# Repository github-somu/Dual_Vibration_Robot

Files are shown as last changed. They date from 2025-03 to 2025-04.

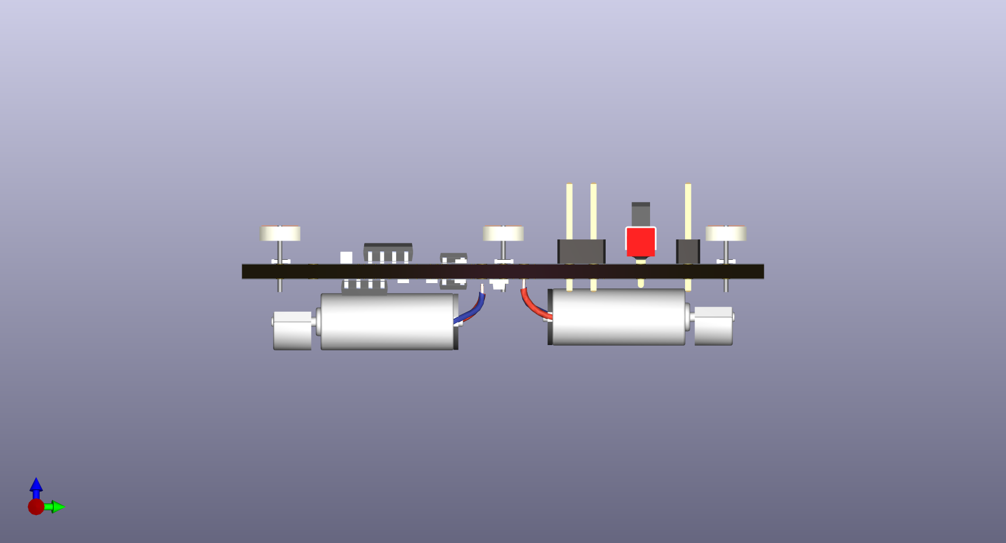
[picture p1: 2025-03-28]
KiCad files/SideViewPCB.png

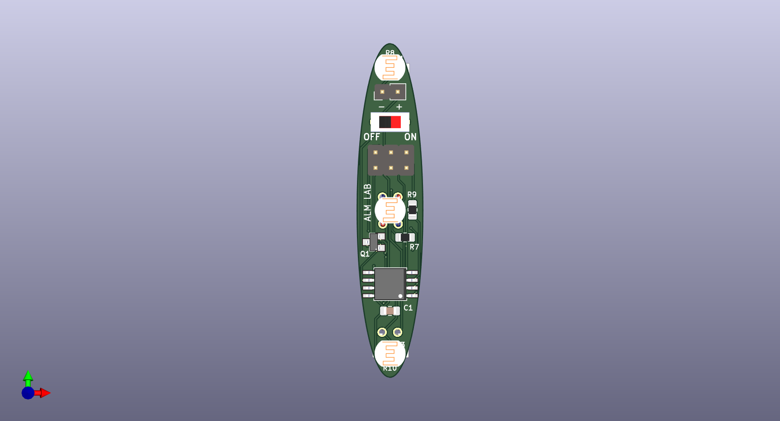
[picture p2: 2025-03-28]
KiCad files/TopViewPCB.png

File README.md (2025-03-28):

# Dual_Vibration_Robot
 This repository contains files related to circuit diagrams, PCB, and 3D models
# Accessing PCB design files and Circuit diagram
Download the KiCad files folder as a .zip file and save it on your computer. After that, extract the folder. Then, the files will open appropriately in KiCad software.

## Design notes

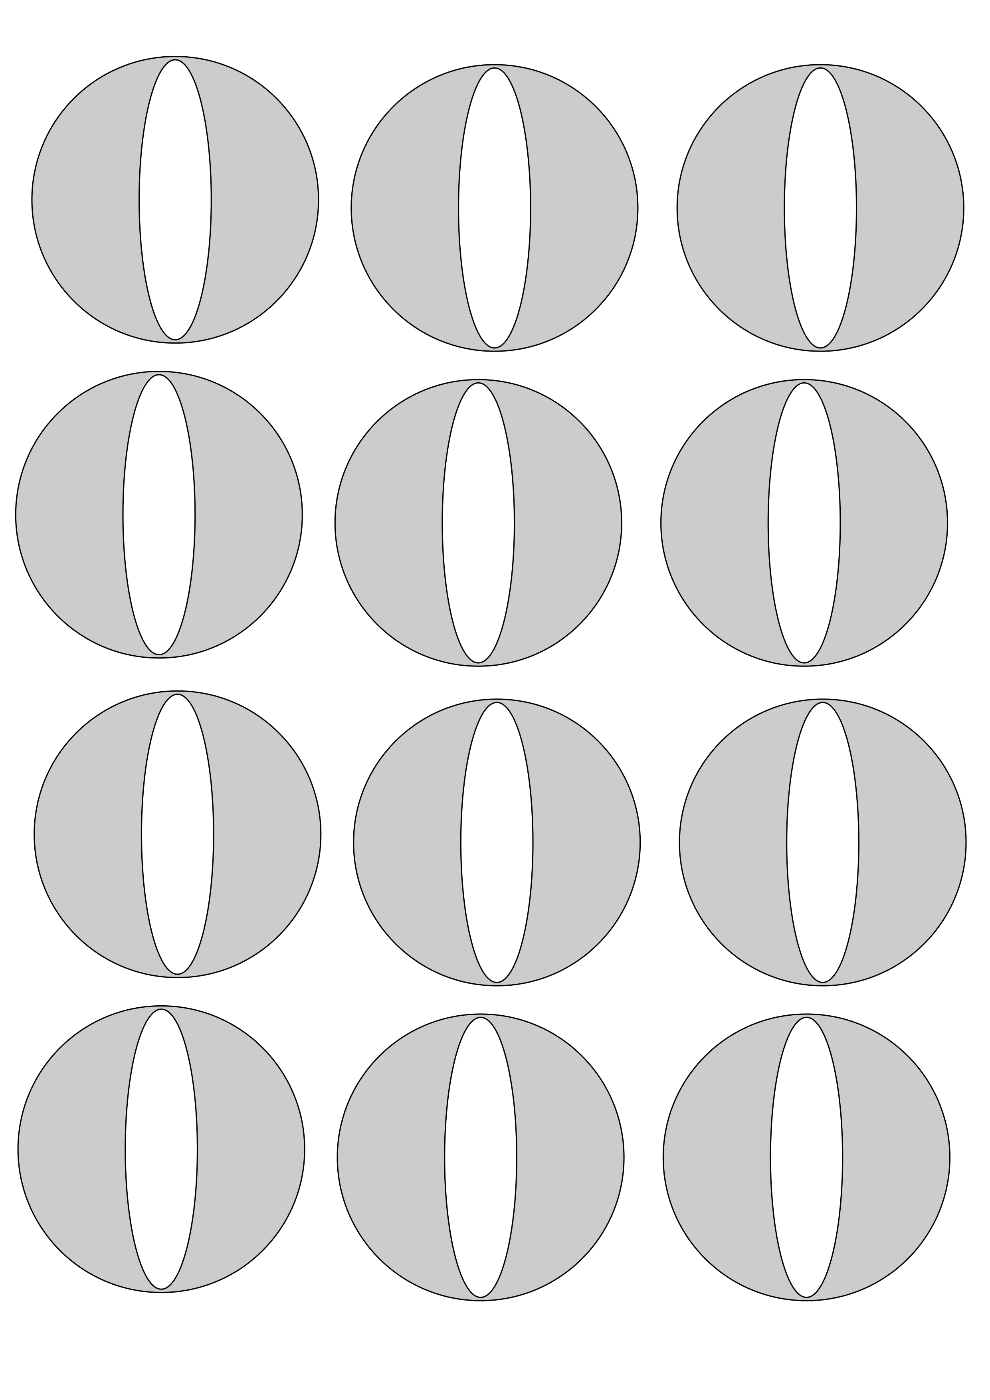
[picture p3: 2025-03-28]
3D_models/Circular_body_paper_cove.png

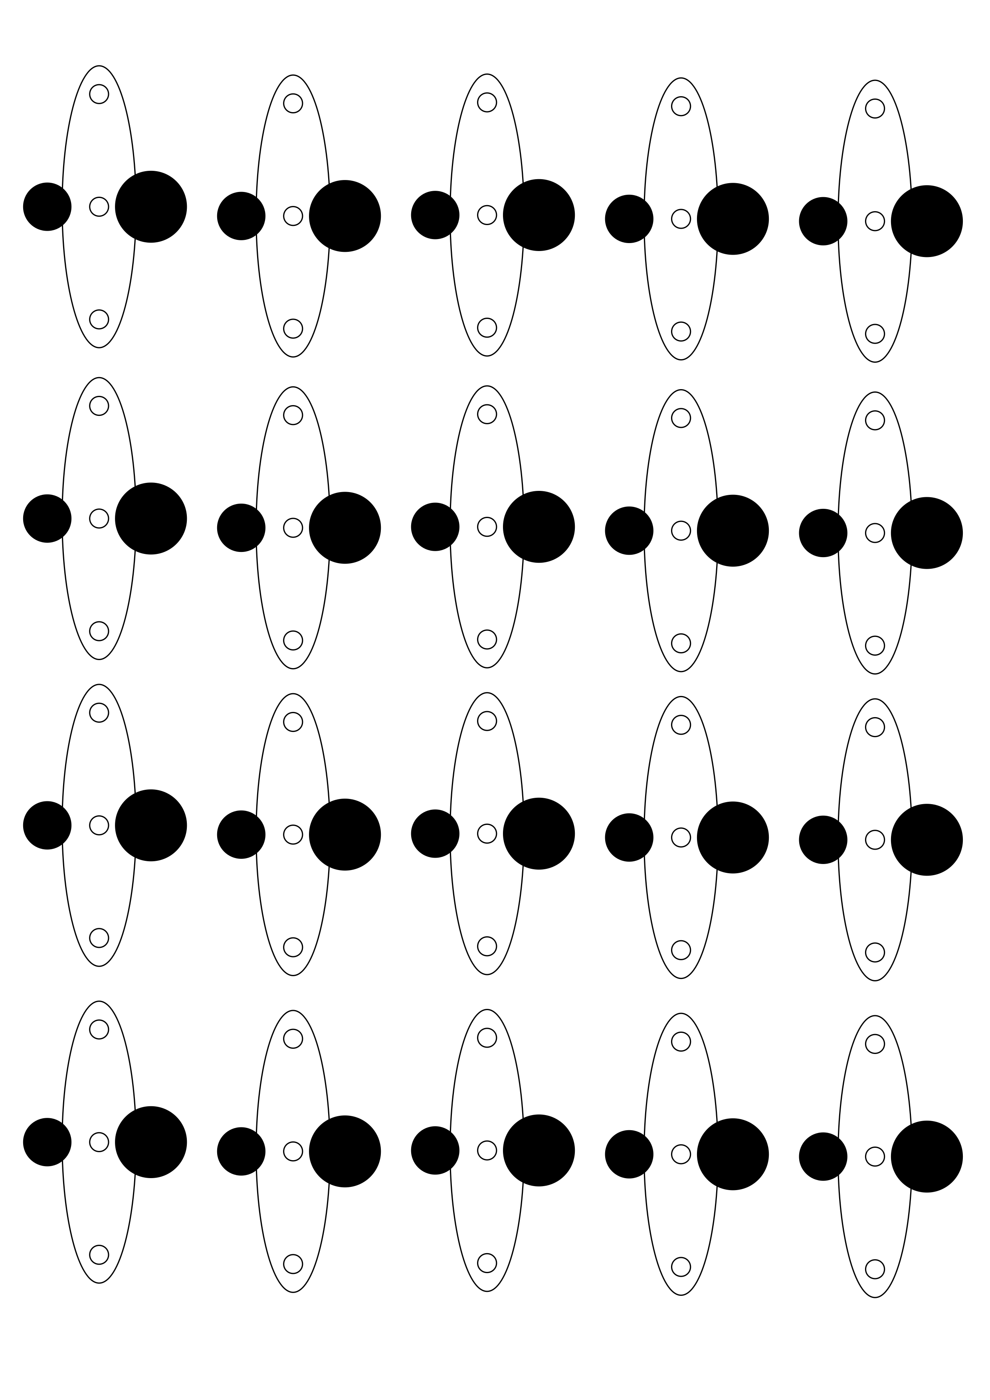
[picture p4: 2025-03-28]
3D_models/Cap_paper_cover.png

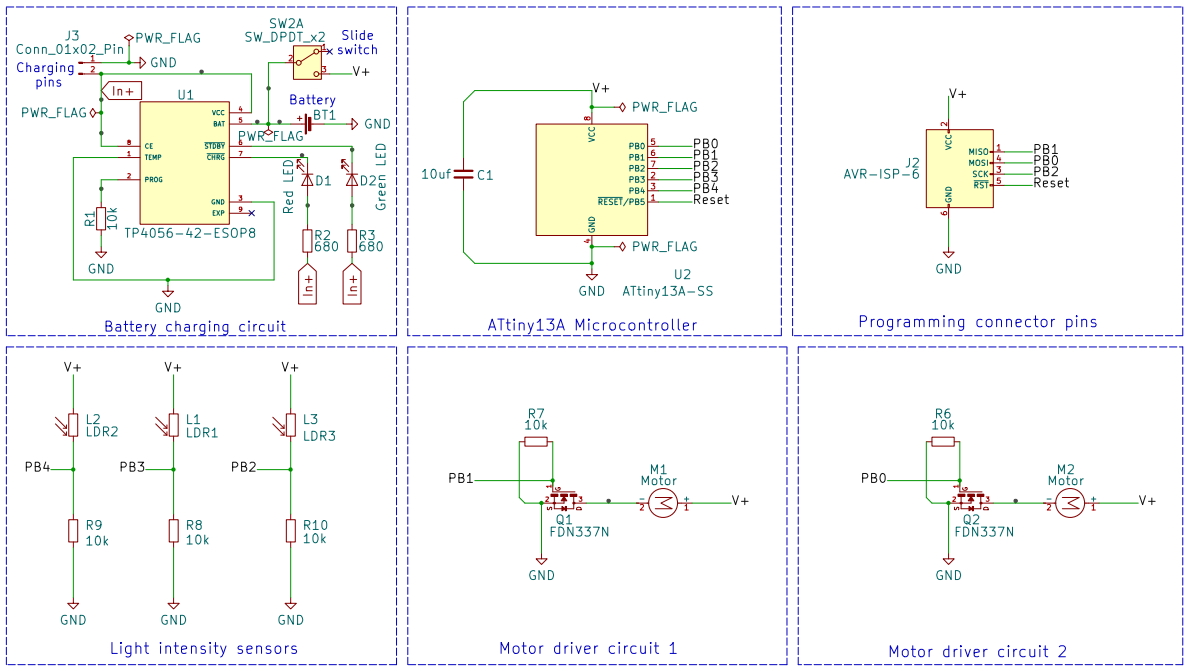
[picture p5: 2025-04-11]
KiCad files/Circuit.png

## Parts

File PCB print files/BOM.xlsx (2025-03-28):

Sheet: SingleMotor
Sample - Bill of Material
Sr. No. | Quantity | Reference | Value | Part Type | PCB Footprint | Manufacturer Part Number/ Generic Part Number[PCB Power] | Manufacturer Name | Description
1 | 5 | R1, R7, R8, R9, R10 | 10 komh, 125mW | Resistor | SMD0805 | GPR080510K | Generic Components - PCB Power | SMD Chip Resistor, 10 kohm, ± 1%, 125 mW, 0805 [2012 Metric], Thick Film, General Purpose
2 | 2 | R2, R3 | 4.7 komh, 125mW | Resistor | SMD0805 | GPR08054K7 | Generic Components - PCB Power | SMD Chip Resistor, 4.7 kohm, ± 1%, 125 mW, 0805 [2012 Metric], Thick Film, General Purpose
3 | 1 | C1 | 10uF, 35V | Capacitor | SMD0805 | GPC0805106-35 | Generic Components - PCB Power | Multilayer Ceramic Capacitors MLCC - SMD/SMT Multilayer Ceramic Capacitors MLCC - SMD/SMT 0805 10uF 35volts *Derate Voltage/Temp
4 | 1 | U2 | NA | ATtiny13A | SOIC127P798X216-8N | ATtiny13A-SU / ATtiny13A-SUR / ATtiny13A-SH / ATtiny13A-SHR | Microchip Technology (https://www.mouser.in/manufacturer/microchip/) | 8-bit Microcontrollers - MCU 1KB In-system Flash 20MHz 1.8V-5.5V
5 | 1 | Q2 | NA | n-MOSFET | SSOT-3 | FDN337N | onsemi / Fairchild | MOSFET SSOT-3 N-CH 30V
6 | 1 | D2 | NA | LED-G | SMD0805 | HSMM-C170 (https://www.mouser.in/ProductDetail/Broadcom-Avago/HSMM-C170?qs=YDL0qNrpDT515hwcVWI5gg%3D%3D) | Broadcom / Avago (https://www.mouser.in/manufacturer/broadcom/) | Standard LEDs - SMD Green Diffused 525nm 120mcd
7 | 1 | D1 | NA | LED-R | SMD0805 | HSMH-H170 (https://www.mouser.in/ProductDetail/Broadcom-Avago/HSMH-H170?qs=Li%252BoUPsLEns3UdNxsKqV%252Bg%3D%3D) | Broadcom / Avago (https://www.mouser.in/manufacturer/broadcom/) | Standard LEDs - SMD 0805 Top Mount Mono-Color ChipLED, AllnGaP Red
8 | 1 | U1 | NA | Battery Charging IC | SOIC127P600X175-9N | TP4056-42-ESOP8 | TOPPOWER(Nanjing Extension Microelectronics) | ESOP-8 Battery Management ICs ROHS

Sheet: DoubleMotor
Sr. No. | Quantity | Reference | Value | Part Type | PCB Footprint | Manufacturer Part Number/ Generic Part Number[PCB Power] | Manufacturer Name | Description
1 | 6 | R1, R6, R7, R8, R9, R10 | 10 komh, 125mW | Resistor | SMD0805 | GPR080510K | Generic Components - PCB Power | SMD Chip Resistor, 10 kohm, ± 1%, 125 mW, 0805 [2012 Metric], Thick Film, General Purpose
2 | 2 | R2, R3 | 3.3 komh, 125mW | Resistor | SMD0805 | GPR08054K7 | Generic Components - PCB Power | SMD Chip Resistor, 4.7 kohm, ± 1%, 125 mW, 0805 [2012 Metric], Thick Film, General Purpose
3 | 1 | C1 | 10uF, 35V | Capacitor | SMD0805 | GPC0805106-35 | Generic Components - PCB Power | Multilayer Ceramic Capacitors MLCC - SMD/SMT Multilayer Ceramic Capacitors MLCC - SMD/SMT 0805 10uF 35volts *Derate Voltage/Temp
4 | 1 | U2 | NA | ATtiny13A | SOIC127P798X216-8N | ATtiny13A-SU / ATtiny13A-SUR / ATtiny13A-SH / ATtiny13A-SHR | Microchip Technology (https://www.mouser.in/manufacturer/microchip/) | 8-bit Microcontrollers - MCU 1KB In-system Flash 20MHz 1.8V-5.5V
5 | 2 | Q1,Q2 | NA | n-MOSFET | SSOT-3 | FDN337N | onsemi / Fairchild | MOSFET SSOT-3 N-CH 30V
6 | 1 | D2 | NA | LED-G | SMD0805 | HSMM-C170 (https://www.mouser.in/ProductDetail/Broadcom-Avago/HSMM-C170?qs=YDL0qNrpDT515hwcVWI5gg%3D%3D) | Broadcom / Avago (https://www.mouser.in/manufacturer/broadcom/) | Standard LEDs - SMD Green Diffused 525nm 120mcd
7 | 1 | D1 | NA | LED-R | SMD0805 | HSMH-H170 (https://www.mouser.in/ProductDetail/Broadcom-Avago/HSMH-H170?qs=Li%252BoUPsLEns3UdNxsKqV%252Bg%3D%3D) | Broadcom / Avago (https://www.mouser.in/manufacturer/broadcom/) | Standard LEDs - SMD 0805 Top Mount Mono-Color ChipLED, AllnGaP Red
8 | 1 | U1 | NA | Battery Charging IC | SOIC127P600X175-9N | TP4056-42-ESOP8 | TOPPOWER(Nanjing Extension Microelectronics) | ESOP-8 Battery Management ICs ROHS

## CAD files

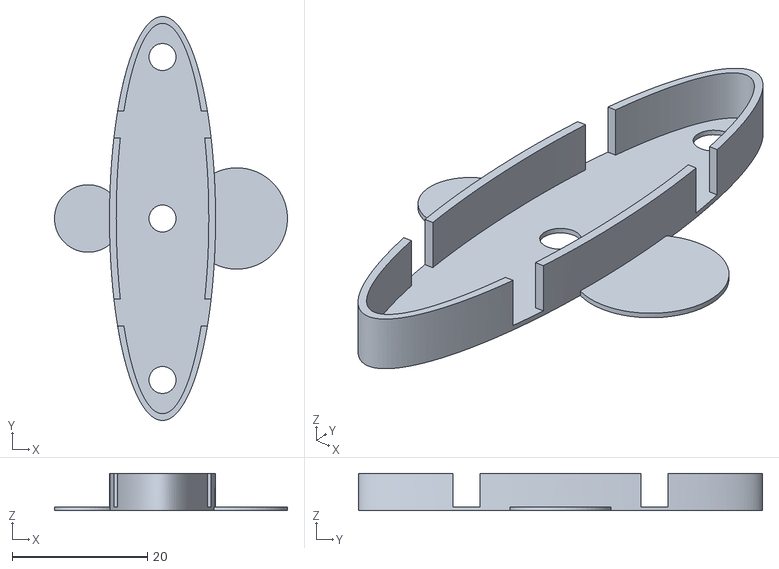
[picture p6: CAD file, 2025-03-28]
3D_models/Cap_DualCircles.stl
34.5 x 59.8 x 5.50

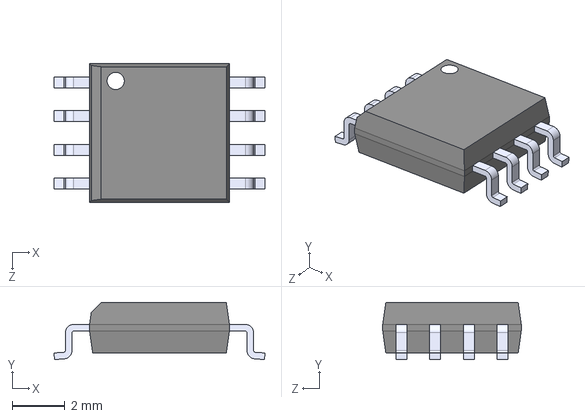
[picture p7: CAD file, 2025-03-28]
KiCad files/ATTINY13A-SSU/ATTINY13A-SSU.step
7.98 x 2.16 x 5.24 mm

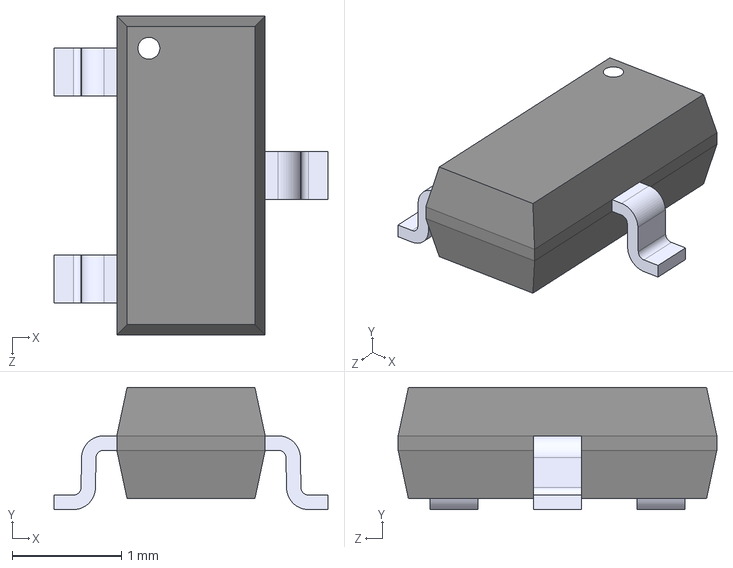
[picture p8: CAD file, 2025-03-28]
KiCad files/FDN337N/FDN337N.step
2.51 x 1.12 x 2.92 mm

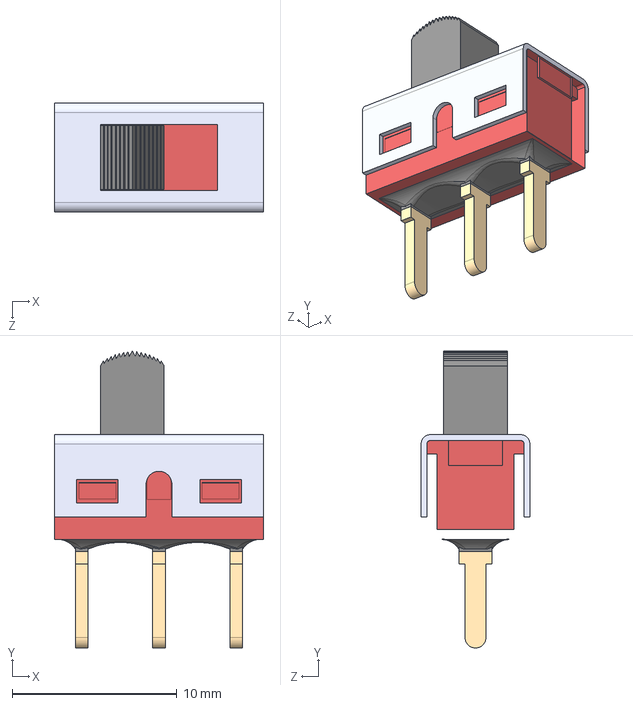
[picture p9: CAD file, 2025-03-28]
KiCad files/STEP files/500SSP1S1M2REA--3DModel-STEP-418109.STEP
12.7 x 18.0 x 6.60 mm

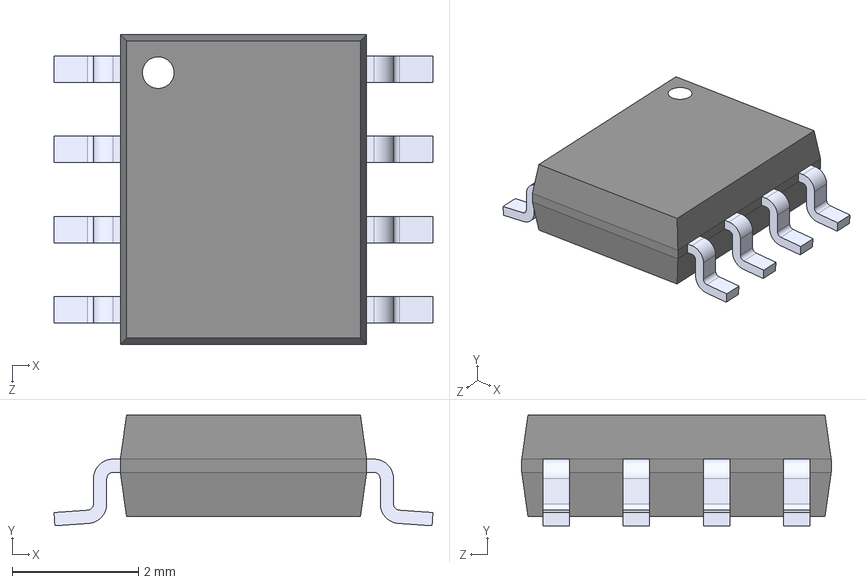
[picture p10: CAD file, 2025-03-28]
KiCad files/TP4056-42-ESOP8/TP4056-42-ESOP8.step
6.00 x 1.75 x 4.90 mm

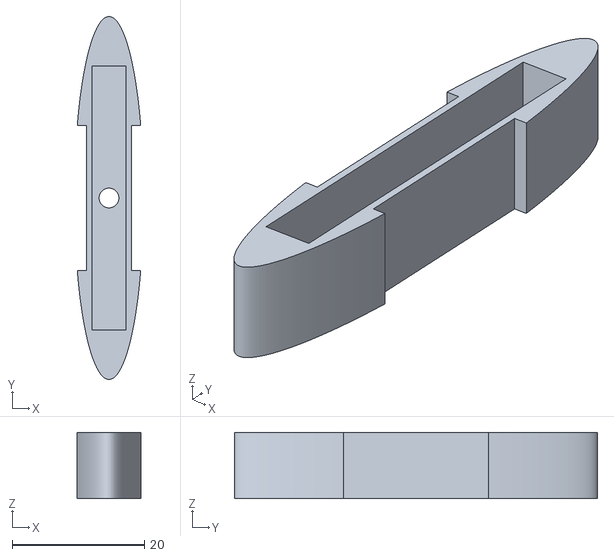
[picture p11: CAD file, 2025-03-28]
3D_models/BattteryHolder_OutwardMotors.stl
9.62 x 55.0 x 10.0

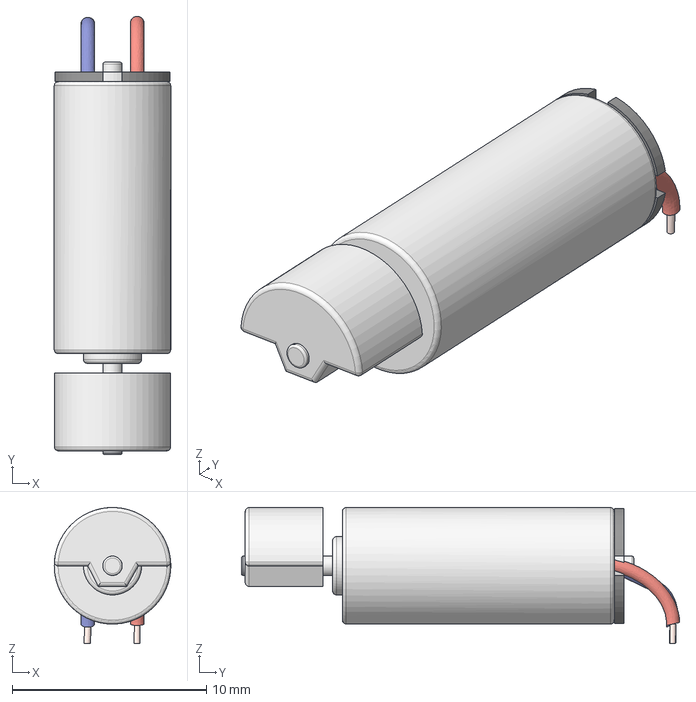
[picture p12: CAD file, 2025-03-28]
KiCad files/STEP files/VibrationMotor v1.step
6.00 x 22.6 x 7.00 mm

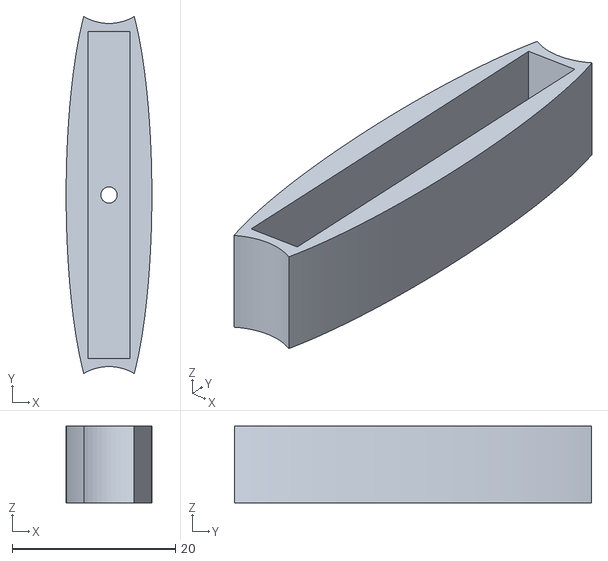
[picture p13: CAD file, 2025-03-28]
3D_models/BatteryHolder_InwardMotors.stl
10.5 x 43.7 x 9.40

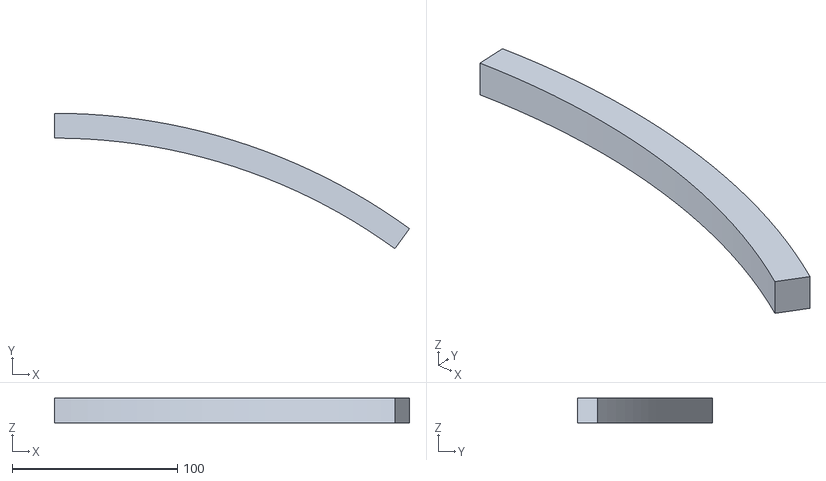
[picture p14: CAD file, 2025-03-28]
3D_models/Boundary_01.stl
214.5 x 81.8 x 15.0

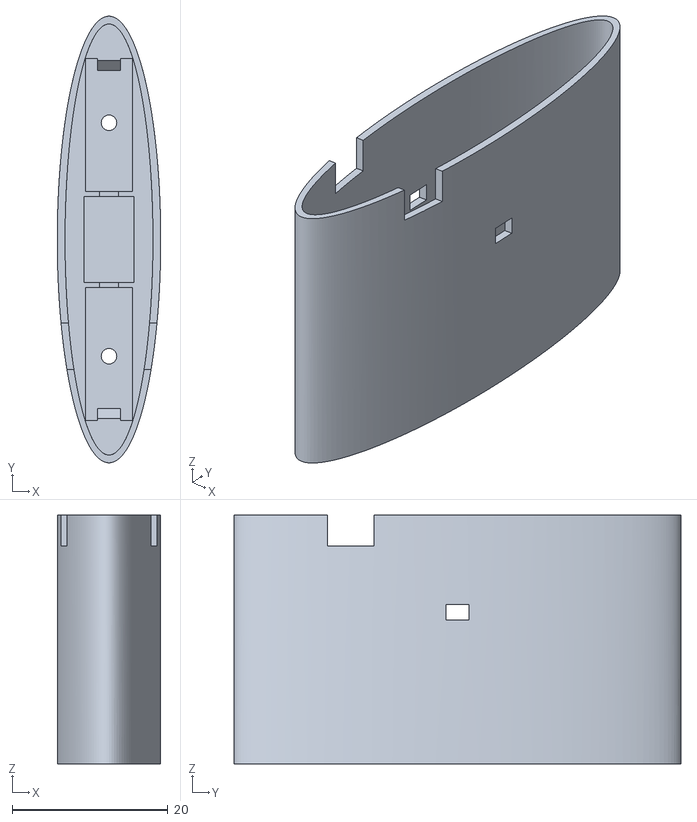
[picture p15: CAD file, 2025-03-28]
3D_models/Body_DualMotor_Inward_Horizontal.stl
13.3 x 57.4 x 32.0

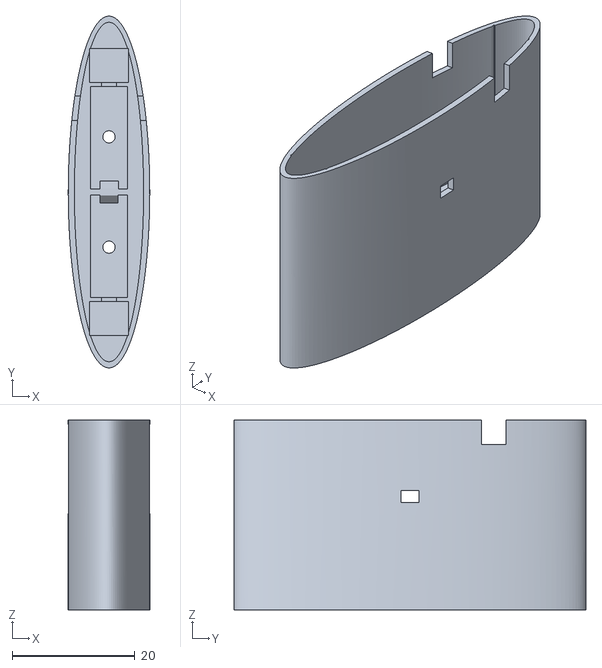
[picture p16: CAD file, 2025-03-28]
3D_models/Body_DualMotor_Outward_Horizontal.stl
13.3 x 57.4 x 31.0

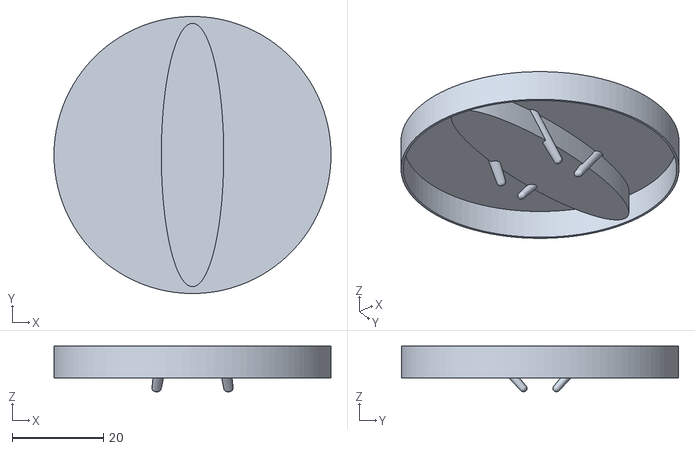
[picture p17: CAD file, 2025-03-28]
3D_models/Legs_Circular.stl
60.8 x 60.8 x 10.0

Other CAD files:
3D_models/Boby_and_BatteryHolder_OutwardMotors.f3d
3D_models/Boundary_Part.f3d
3D_models/Cap_DualCircles.f3d
3D_models/Legs_CircularShape.f3d
3D_models/More_separated_legs v2.f3d

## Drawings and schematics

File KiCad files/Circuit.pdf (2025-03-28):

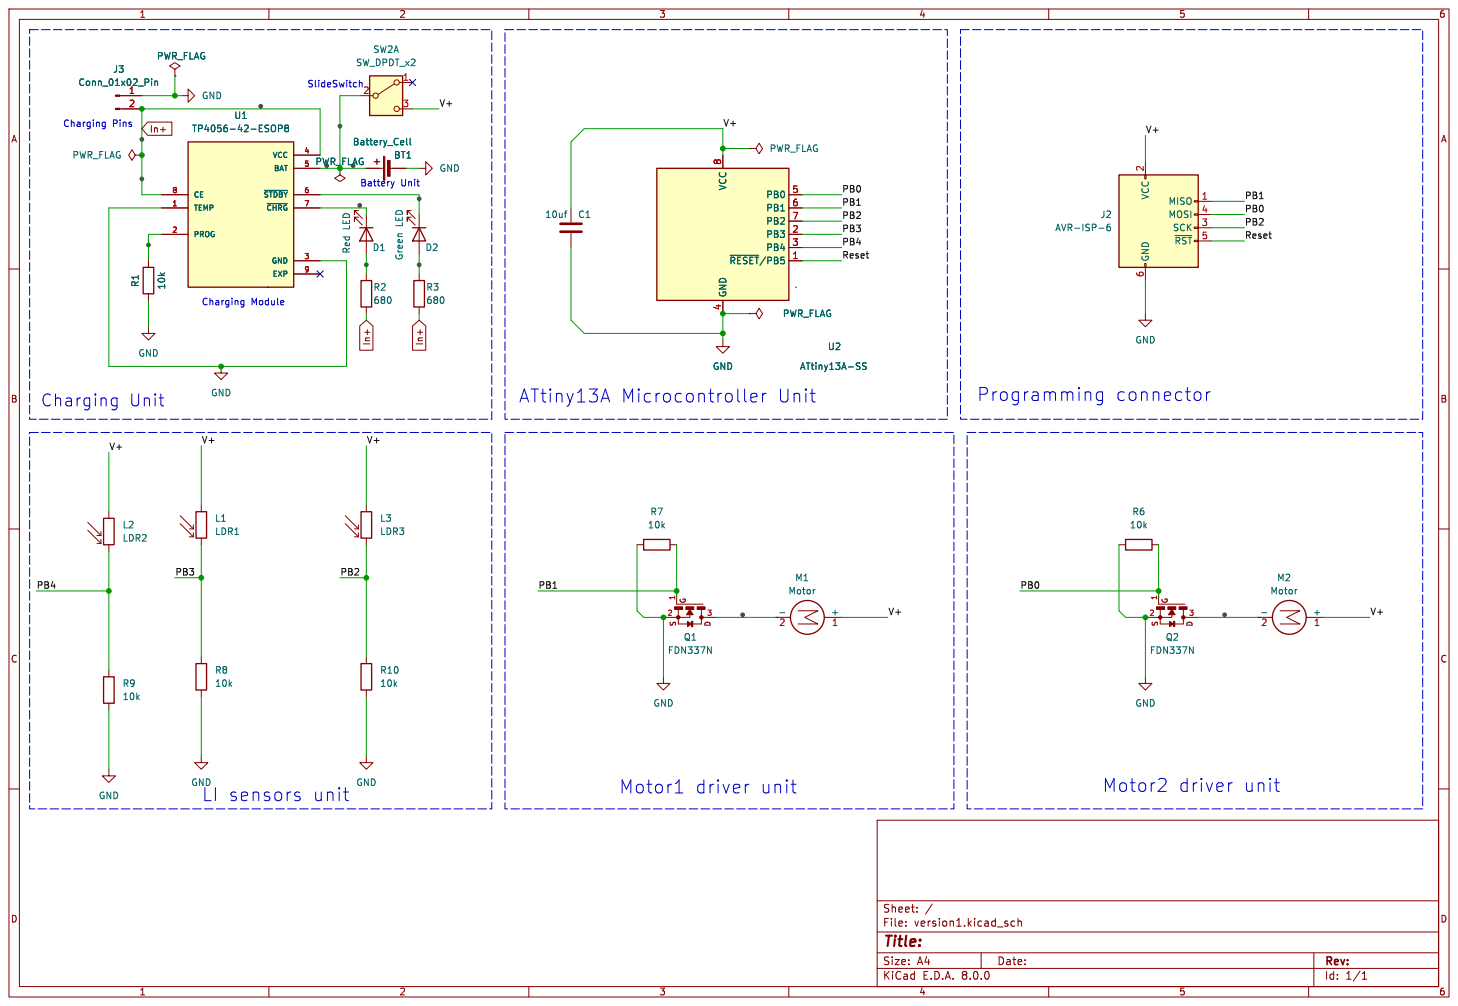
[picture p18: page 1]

2 SCK 3 MOSI 4 ~{RST}5 GND

Id: 1/1 Title: File: version1.kicad_sch Sheet: /

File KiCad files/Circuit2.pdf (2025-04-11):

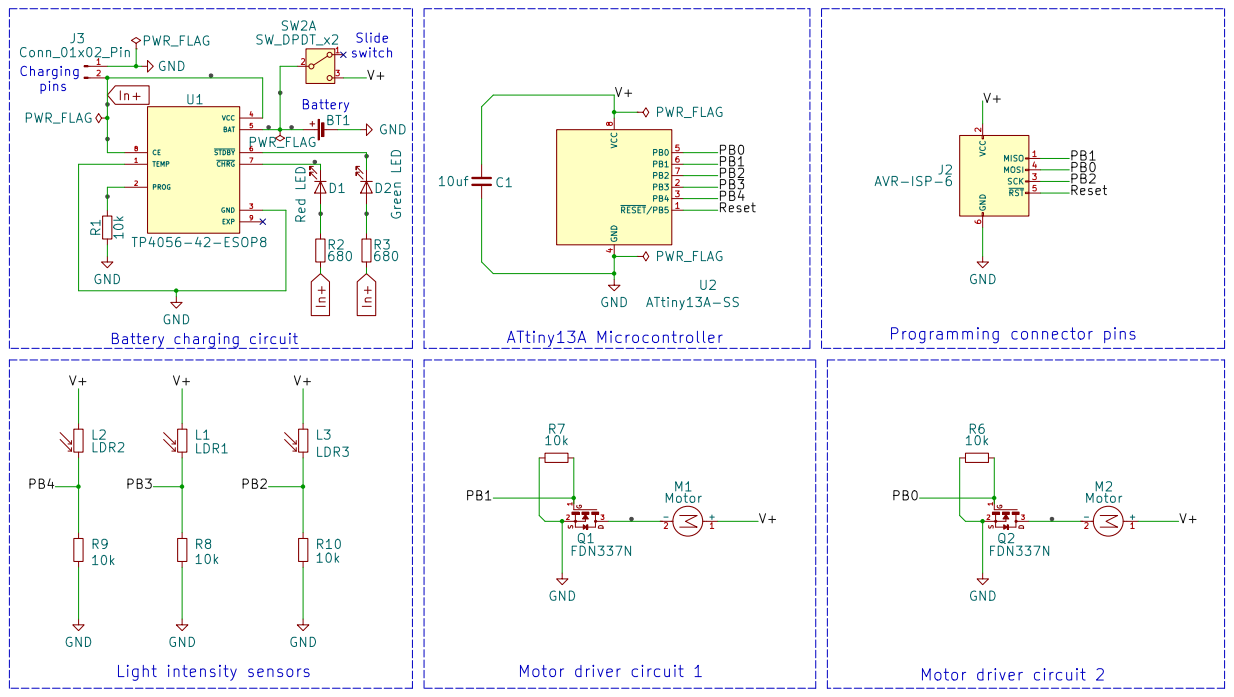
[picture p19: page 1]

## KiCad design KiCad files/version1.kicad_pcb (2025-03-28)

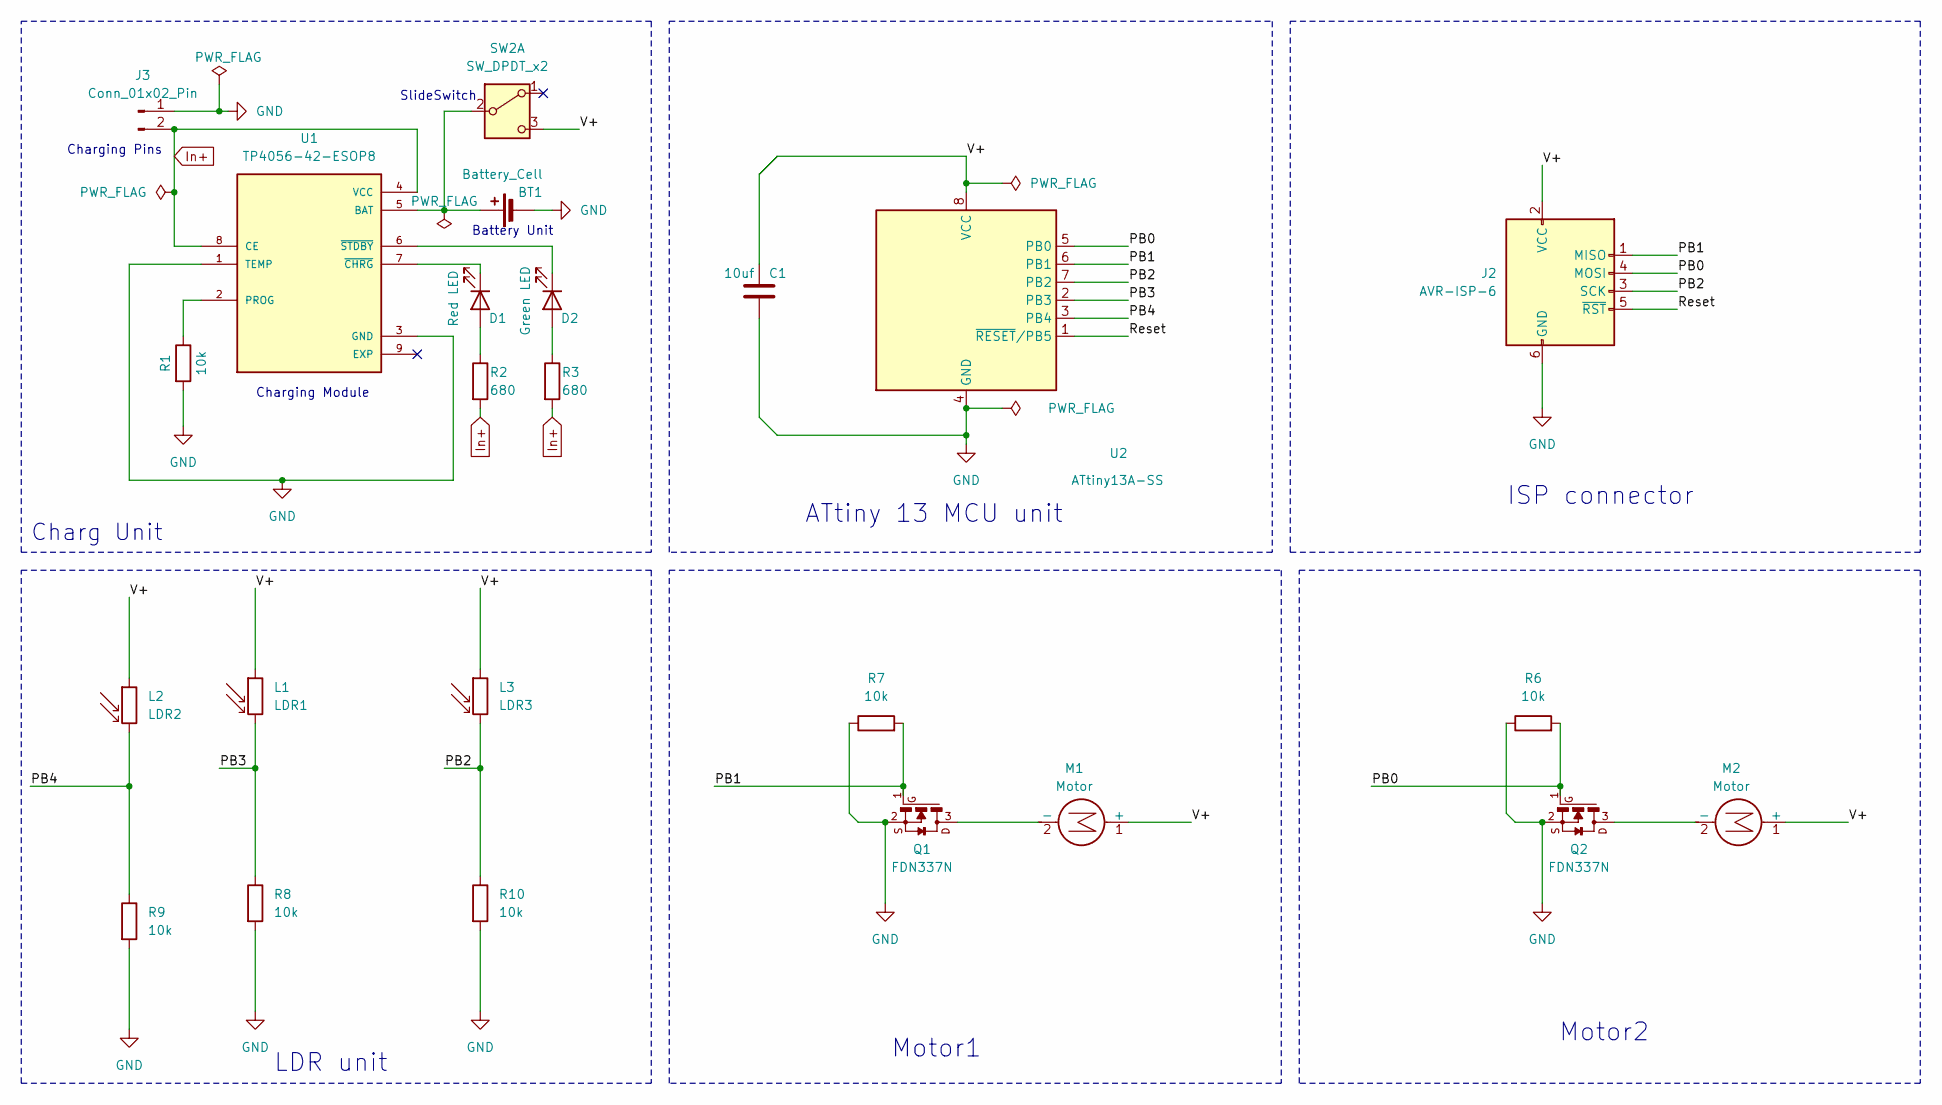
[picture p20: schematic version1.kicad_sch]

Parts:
BT1: Battery_Cell; BatteryHolder_KP401020
C1: 10uf; C_0805_2012Metric_Pad1.18x1.45mm_HandSolder
D1: Red LED; LED_0805_2012Metric_Pad1.15x1.40mm_HandSolder
D2: Green LED; LED_0805_2012Metric_Pad1.15x1.40mm_HandSolder
J2: AVR-ISP-6; IDC-Header_2x03_P2.54mm_Vertical
J3: Conn_01x02_Pin; PinHeader_1x02_P2.54mm_Vertical
L1: LDR1; R_LDR_5.1x4.3mm_P3.4mm_Vertical
L2: LDR2; R_LDR_5.1x4.3mm_P3.4mm_Vertical
L3: LDR3; R_LDR_5.1x4.3mm_P3.4mm_Vertical
M1, M2: Motor; VibrationMotor
Q1, Q2: FDN337N; SSOT-3
R1, R6, R7, R8, R9, R10: 10k; R_0805_2012Metric_Pad1.20x1.40mm_HandSolder
R2, R3: 680; R_0805_2012Metric_Pad1.20x1.40mm_HandSolder
SW2: SW_DPDT_x2; Switch
U1: TP4056-42-ESOP8; SOIC127P600X175-9N; PARTREV NA
U2: ATtiny13A-SS; SOIC127P798X216-8N

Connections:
/PB0: J2.4 (MOSI), Q2.1, R6.2, U2.5 (PB0)
/PB1: J2.1 (MISO), Q1.1, R7.2, U2.6 (PB1)
/PB2: J2.3 (SCK), L3.2, R10.1, U2.7 (PB2)
/PB3: L1.2, R8.1, U2.2 (PB3)
/PB4: L2.2, R9.1, U2.3 (PB4)
/Reset: J2.5 (~RST), U2.1 (~RESET/PB5)
/V+: C1.1, J2.2 (VCC), L1.1, L2.1, L3.1, M1.1 (+), M2.1 (+), SW2.3 (C), U2.8 (VCC)
GND: BT1.2 (-), C1.2, J2.6 (GND), J3.1, Q1.2, Q2.2, R1.2, R6.1, R7.1, R8.2, R9.2, R10.2, U1.1 (TEMP), U1.3 (GND), U2.4 (GND)
In+: J3.2, R2.2, R3.2, U1.4 (VCC), U1.8 (CE)
unnamed: BT1.1 (+), SW2.2 (B), U1.5 (BAT)
unnamed: D1.2 (A), R2.1
unnamed: D1.1 (K), U1.7 (~CHRG)
unnamed: D2.2 (A), R3.1
unnamed: D2.1 (K), U1.6 (~STDBY)
unnamed: M1.2 (-), Q1.3
unnamed: M2.2 (-), Q2.3
unnamed: R1.1, U1.2 (PROG)

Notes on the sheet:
ISP connector
Charg Unit
Motor2
ATtiny 13 MCU unit
LDR unit
Charging Module
SlideSwitch
Battery Unit
Motor1
Charging Pins

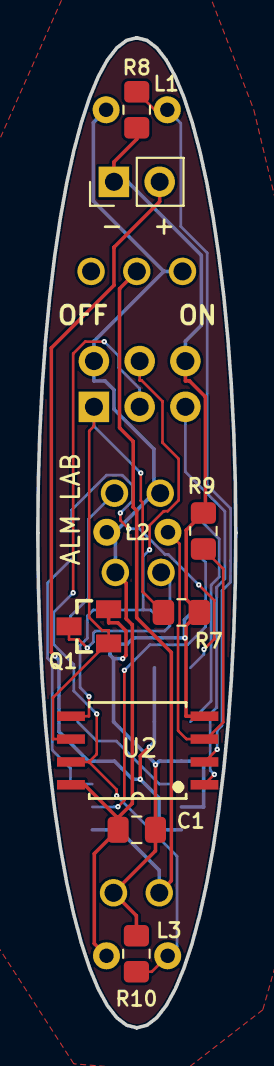
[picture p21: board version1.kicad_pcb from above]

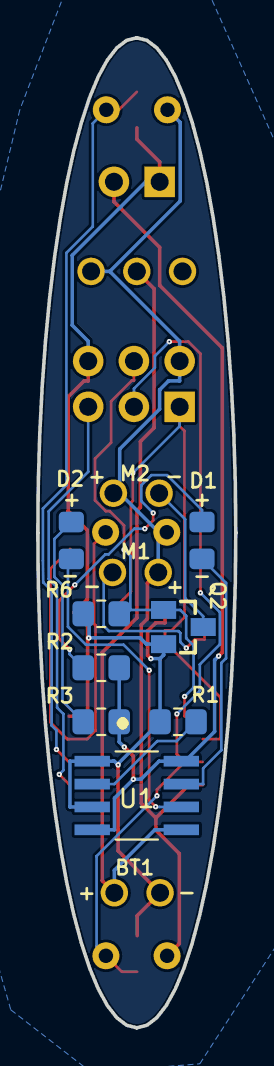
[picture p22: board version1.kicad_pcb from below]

Board: 2 copper layers, 11.0 x 55.0 mm, 24 parts (10 on the bottom side), 17 nets.

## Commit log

2025-03-28 Added the 3D model files
    [BatteryHolder_InwardMotors.stl, BattteryHolder_OutwardMotors.stl, Boby_and_BatteryHolder_OutwardMotors.f3d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]
2025-03-28 Added the KiCad files
    [500SSP1S1M2REA--3DModel-STEP-418109.STEP, ATTINY13A-SSU.STEP, ATTINY13A-SSU.step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]
2025-03-28 Added PCB print files
    [BOM.xlsx, PP.xlsx]
2025-04-11 updated files
    [version1.kicad_sch]
